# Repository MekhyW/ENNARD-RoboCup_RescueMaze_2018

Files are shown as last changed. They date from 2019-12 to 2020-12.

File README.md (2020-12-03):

# ENNARD - RoboCup Rescue Maze 2018
###### Autonomous navigation and victim-identifying robot, created to compete in RoboCup Junior Brazil Open 2018. The robot achieved 1st place out of 17 at the category, claiming the title of national champion.

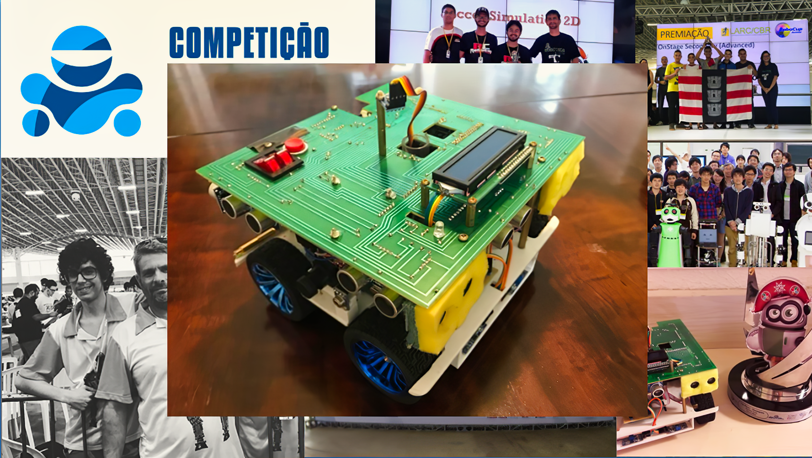
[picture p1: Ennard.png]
Ennard
### 

## Rescue Maze Preface

Rules can be found at: https://junior.robocup.org/rcj-rescue-maze/

" The robot needs to search through a maze for victims. The robot should not find the fastest path through the maze, instead it should explore as much of the maze as possible . The robot will get points for each victim found and will deliver a rescue kit close to the victim. The robot must avoid areas with a black floor.

Rescue Maze sub-league open to students from age 13 up to and including 19 years of age (age as of 1st of July).Team members may compete in Rescue Line twice (2 international events). After competing in Rescue Line twice, they must move to Rescue Maze. "

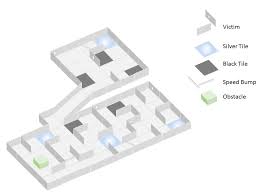
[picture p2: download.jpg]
Arena


## CAD Models

The folder 'models' contains all 3D files used and made during the prototyping/simulation phase of the project, using AutoCAD 2017.  Drawing-SALLES_X.dwg refers to different versions of the robot concept, while pá_X.dwg is a custom servo shovel design to facilitate rescue kit dropping. 

All printable files are in .stl files, and they are mechanically self-sufficient for the static assembly of the entire robot structure (aside from screws, standoffs, etc.).

## Hardware Components

The robot consists of:

1. 1x Arduino DUE microcontroller ARM board
2. 2x OpenMV Cam M7 machine vision boards (UART communication with the Arduino)
3. 4x Pololu 25D 12V HP metal gearmotors with 47:1 reduction (210RPM)
4. 4x Rotary hall-effect motor encoders
5. 4x Rubber wheels
6. 9x HC-SR04 ultrassonic rangefinder sensor modules
7. 2x MLX90614 infrared temperature sensor modules
8. 1x MPU6050 accelerometer sensor module
9. 1x HMC5883l magnetometer sensor module
10. 2x TCRT5000 active light reflectance sensor modules
11. 1x 16x2 segments LCD display with blue backlight
12. 1x Digital arcade button
13. 2x 12V LiPO batteries

## Team Description Paper 

In order to attend the Latin American Robotics Competition, every team must submit a TDP which shows the engineering strategies implemented. The following text (written in Brazillian Portuguese) summarizes these points in the IEEE text format: 'TDP' ---> TDP.pdf / TDP.docx

## Software

Code that is run during scored runs is stored in the 'ENNARD' folder. ENNARD.ino is the main C++ script, while low-level component interactions are handled by each header file.

'TestModes' contains debugging scripts for each component, and 'Cams' contains the multiple strategies tested for the identification of the new "Visual victims" (H, S and U letters), including template matching and blob segmentation.  

## Video Material

A few proof-of-concept videos were produced:

* Final version of the lower part of the chassis ---> https://www.youtube.com/watch?v=Bfc4bDW7wJo

- Wall Alignment (top view) ---> https://www.youtube.com/watch?v=RuqlHey5neY

- Wall Alignment (side view) ---> https://www.youtube.com/watch?v=VqffBqsZt2Q

- PID Control and ramp negotiation ---> https://www.youtube.com/watch?v=kQnzG5W4b-0

- Mecanum omnidirectional wheels (later changed to rubber wheels) ---> https://www.youtube.com/watch?v=znJ_pU6Sihw

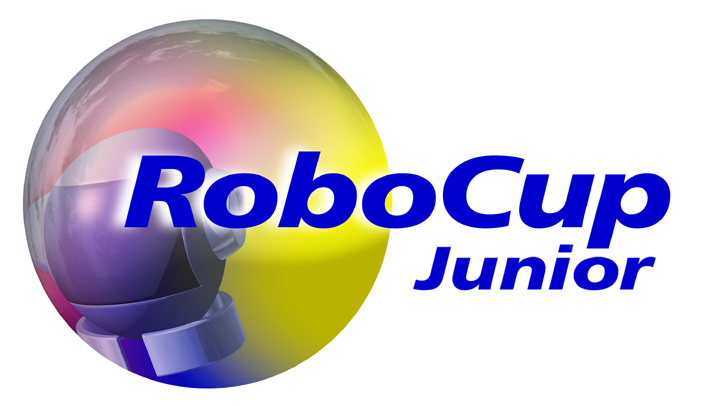
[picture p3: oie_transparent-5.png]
robocupjr


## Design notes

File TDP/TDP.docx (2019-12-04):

ENNARD – Robô de Rescue Maze da Escola de Robótica e Mecatrônica ABC Marcelo Salles

Felipe Catapano Emrich Melo, André Luiz Buzacarini Schulman, Marcelo Ribeiro Salles

Abstract ⎯ This article presents the development of an Arduino-controlled autonomous junior robot with emphasis on Latin American Robotics Competition 2018. All key components and critic design choices, as well as their purposes are detailed in this document.

I. INTRODUÇÃO

Pelo fato de estarmos iniciando na categoria e por complicações nas circunstâncias e envolvendo o projeto, nosso robô competidor para a LARC de 2017 (edição ocorrida em Curitiba, PR) fora construído com diversos problemas estruturais e soluções improvisadas. Utilizávamos motores de plástico energizados por um pack de pilhas (rompido internamente no meio da competição e consequentemente anulando uma de nossas rodadas), que eram fracos e tinham sua movimentação controlada por tempo (o que gerava um alto grau de imprecisão variável). Além disso a disposição dos sensores formava grandes pontos cegos.

Havendo, no entanto, superadas muitas das dificuldades e havendo observado inúmeros outros projetos de âmbito internacional em várias competições, o novo agente foi desenvolvido com a solução por completo da missão proposta em mente, que envolve a simulação de um salvamento de vítimas quentes e visuais em um ambiente de desastre inacessível a seres humanos.

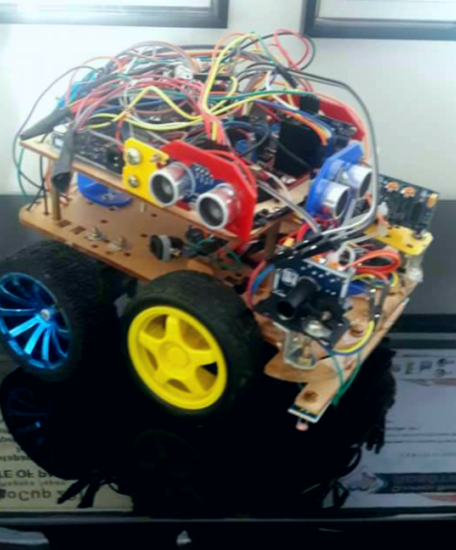
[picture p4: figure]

Imagem 1 - LESION, o robô de 2017

II. ESTRUTURA E CIRCUITOS

Com a utilização de uma impressora 3D, somos capazes de projetar e criar estruturas com encaixes perfeitos para os componentes de forma rápida e barata, portanto o chassi do robô foi desenhado com o software AutoCAD e impresso em PLA amarelo. O tubo e kits do nosso depositador de resgate, no entanto, foram feitos em acrílico para que não houvesse qualquer rebarba.

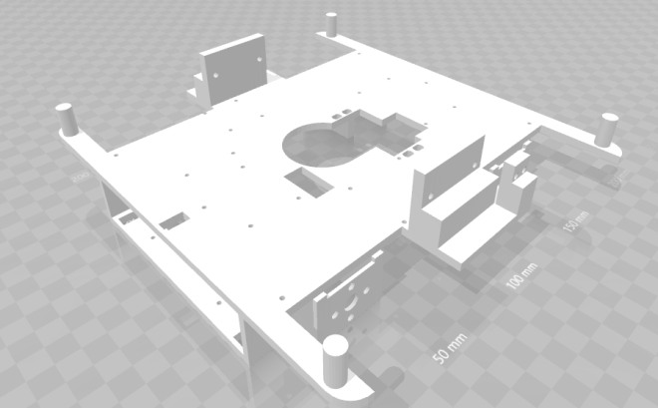
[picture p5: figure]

Imagem 2 - Chassi

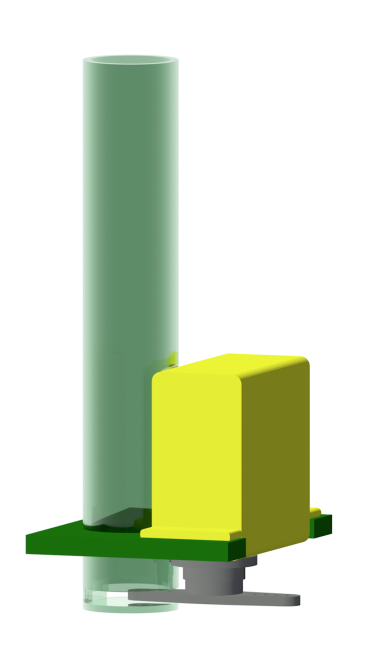
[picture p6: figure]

Imagem 3 - Depositador

Para similar finalidade, a de reduzir ao máximo a quantidade de fios e evitar problemas facilmente, percebemos que a impressão de circuitos integrados era essencial (também a desenhamos com AutoCAD). Duas PCBs ligadas por grupos de flat cables permitem que todas as trilhas possuam 1cm de largura e sejam consideravelmente expostas, reduzindo a possibilidade de erros.

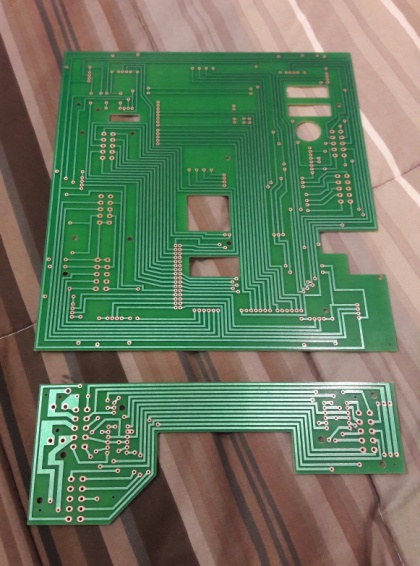
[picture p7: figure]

Imagem 4 – Circuitos integrados (primeiros protótipos)

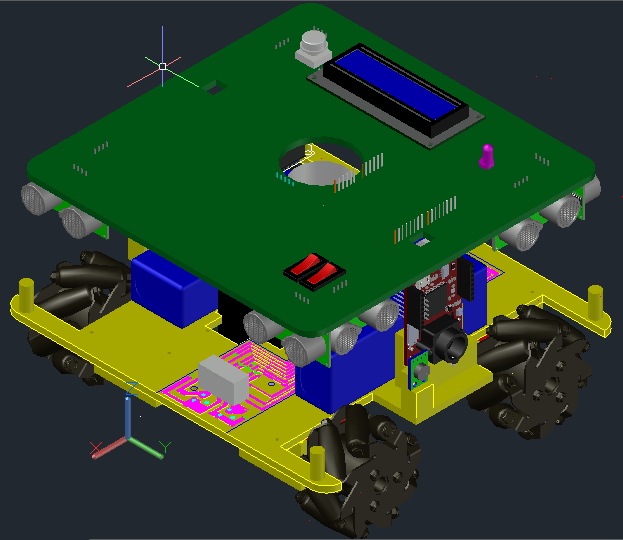
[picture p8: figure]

Imagem 5 – Robô completo simulado em CAD

III. CONTROLE E ATUAÇÃO

Arduino DUE foi a plataforma central escolhida pela simplicidade de uso, maior capacidade de variáveis e maior velocidade em relação a todos os outros arduinos, além da possibilidade de utilizar qualquer pino digital com interrupts, para melhor aproveitamento dos encoders presentes nos motores por exemplo (é a única placa da Arduino com arquitetura ARM). Ela (juntamente com os sensores conectados) é alimentada por um pack de baterias de Li-Ion, enquanto os motores são controlados por duas pontes-h L298n alimentadas em série por uma bateria de Li-Po separada.

Grande parte de nossa estratégia se dá pela escolha dos motores DC de 12V da Pololu, colocando a qualidade de alinhamento sensorial e velocidade de ultrapassagem de obstáculos acima da precisão absoluta garantida por servos motores. Um servo motor genérico MG996R (visto no suporte acima) foi utilizado para o depósito dos kits de resgate pelo baixo peso e custo para seu tamanho.

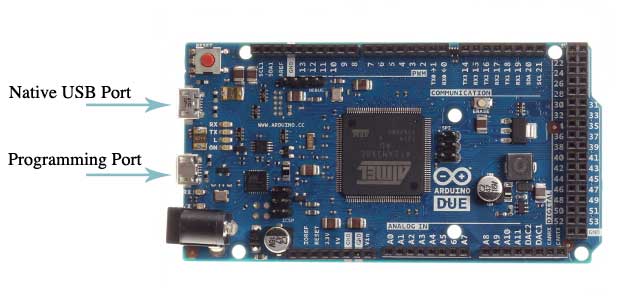
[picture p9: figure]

Imagem 6 – Arduino DUE

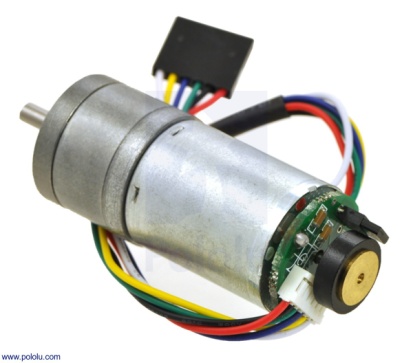
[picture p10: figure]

Imagem 7 – Motor com encoder

E para que fosse possível garantir total liberdade de movimento ao robô, as rodas ligadas aos motores são rodas mecanum da Nexus, de 6cm de diâmetro, adaptadas por calços usinados customizados para este fim. Seus rolos dispostos em 45 graus permitem a mesma característica de um sistema com quatro rodas omni tradicionais: Facilmente mover-se em qualquer direção (útil para alinhamentos rapidos e movimentos pequenos), porém com o benefício de poderem ser dispostas de maneira reta como rodas comuns.

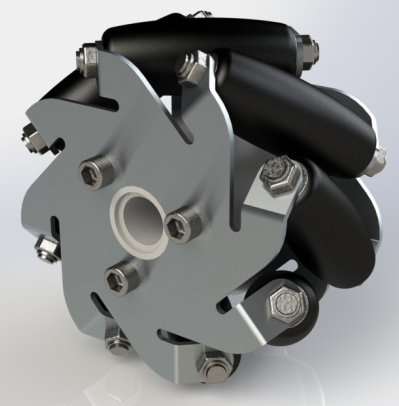
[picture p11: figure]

Imagem 8 – Roda mecanum

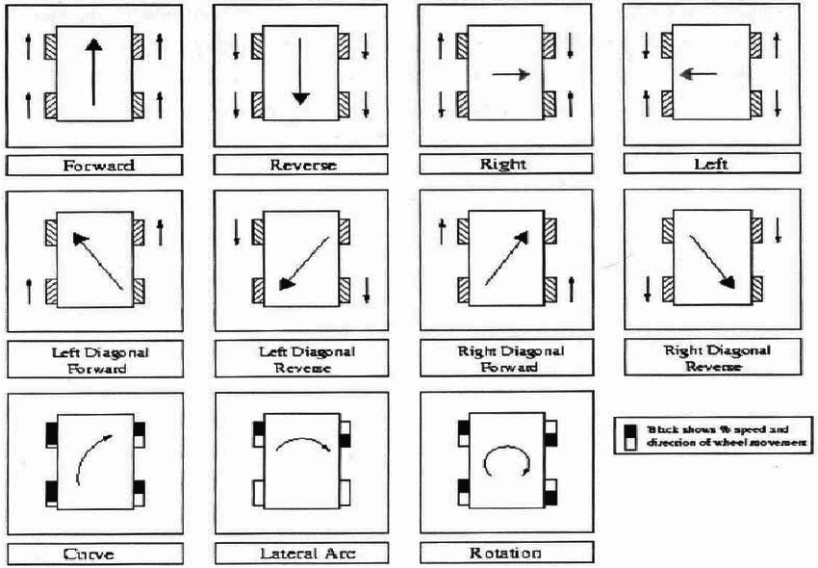
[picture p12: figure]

Imagem 9 – Esquema de movimentação com 4 rodas mecanum

IV. SENSORES E SINALIZAÇÃO

Para possibilitar a identificação das novas vítimas visuais, utilizamos duas pequenas placas programáveis OpenMV M7, ligadas ao arduino por comunicação UART. Por possuírem conexão externa e uma IDE própria, calibrar as placas pode ser feito de maneira direta e é possível retirá-las do robô facilmente caso necessário.

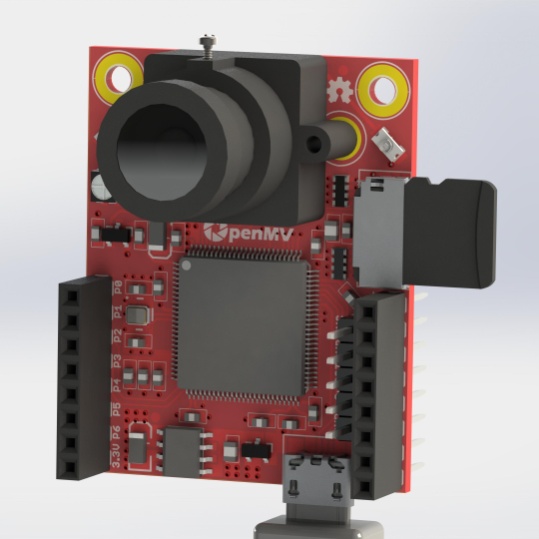
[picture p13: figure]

Imagem 10 – OpenMV com cartão SD

Escolhemos usar nove sensores ultrassônicos US-015 dispostos na horizontal para o sensoriamento das paredes pelo seu amplo campo de visão e precisão de medida acima dos comuns HC-SR04. Por suportarem o uso de interrupts digitais e não precisarmos ler todos as instâncias de uma única vez, seu elevado delay em relação a um sensor de luz torna-se desprezível.

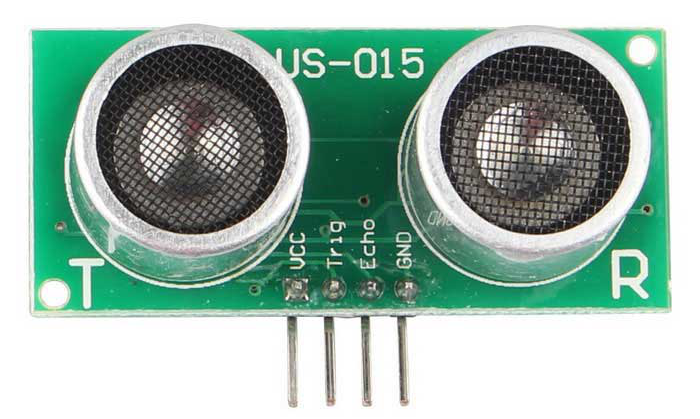
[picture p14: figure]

Imagem 11 – Sensor ultrassônico

A medição inercial é realizada por um único módulo 10DOF, o GY-87, que reúne giroscópio, acelerômetro(MPU6050, utilizado para percepção da rampa) e magnetômetro(HMC5883l, utilizado como bússola), além de um barômetro.

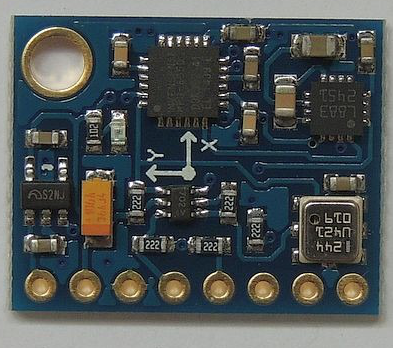
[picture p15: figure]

Imagem 12 – Unidade de Medição Inercial (UMI)

Para completar o sensoriamento utilizamos os populares MLX90614 para o reconhecimento das vítimas quentes, e dois sensores TCRT5000 para refletância do solo (perceber tiles pretos e tiles de checkpoint), além dos encoders presentes nos motores.

Há uma tela LCD de 16x2 divisões para feedback por texto, o que dispensa a constante necessidade de manter uma conexão com o computador para rastrear alguma variável ou processo, além de um LED multicolorido para sinalizar ações ao juíz e ao capitão da equipe com apenas um único sinal.

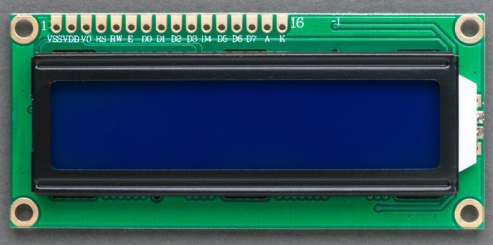
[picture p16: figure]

Imagem 13 – Display com luz de fundo azul

V. O SOFTWARE

Toda a programação do arduino foi escrita com a linguagem C++ utilizando o editor de texto Sublime Text 3 e compilada com a ArduinoIDE. Esta visa uma movimentação rápida e totalmente contínua do robô (isto é, sem um único delay) com alinhamentos constantes em relação às paredes. Um algoritmo de controle Proporcional Integral Derivativo (PID) será implementado para manter o robô centralizado ao subir e descer as rampas.

Um filtro Low Pass é aplicado na maioria das leituras para que não haja muitos ruídos entre as mesmas, e .

Para o path planning (decisão de quais direções a tomar dentro do labirinto), utilizamos o algoritmo de Tremaux como base (virar à direita é priorizado em relação a seguir em frente ou virar à esquerda, com objetivo de “contornar” o mapa), e a complementamos com um algoritmo de Floodfill modificado (priorização de áreas ainda não exploradas na rodada e retorno ao quadrado inicial pelo caminho mais curto conhecido, sem a necessidade de rotinas secundárias ou um mapeamento da configuração do labirinto). Na partida, Um mapa virtual é criado com todos os nodos incialmente zerados, e, após o robô passar de um nodo a outro, caso o valor deste for zero ele passa a ser o sucessor do valor do nodo anterior.

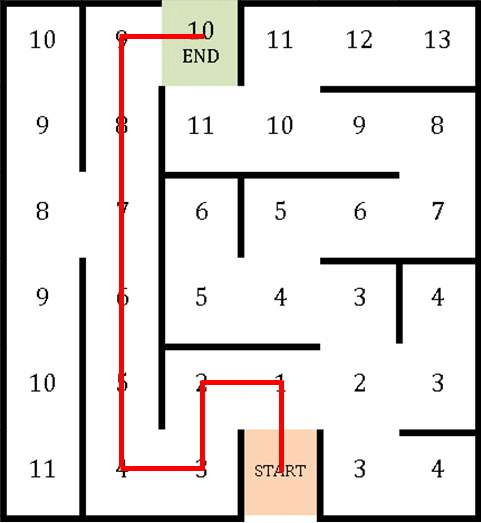
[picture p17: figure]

Imagem 14 – Exemplo de FloodFill resolvendo um labirinto com saída

A programação das câmeras é escrita em Python (elas funcionam com o sistema operacional MicroPython) pela própria IDE da OpenMV, e consiste na comparação entre cada frame capturado pelo módulo embutido e pequenas fotos de letras presentes na memória flash (algoritmo conhecido como Template Matching). Parâmetros básicos de imagem como exposição, equilíbrio de branco, etc.são automaticamente normalizados pela câmera, assim reduzindo todos os parâmetros humanamente ajustados a apenas três filtros de 0 a 1, um para cada letra a ser identificada.

VI. ARENA DE TESTES

Percebemos durante o planejamento deste projeto que a construção de um ambiente que simule situações oficialmente presente nas competições é essencial para uma boa preparação da estratégia. Portanto a equipe investiu em uma arena que seguisse fielmente as regras, apesar do seu real tamanho quando montada, para podermos testar aspectos do robô antes mesmo de este estar funcionando por completo.

A madeira é o material ideal utilizado na grande maioria desses eventos pelo seu baixo custo, resistência e facilidade de produzir encaixes lineares. Portanto toda a estrutura da arena de testes é feita com este material. Lombadas, garrafas de areia, tijolos, varetas e outros obstáculos estão a disposição para criar cenários com um nível de desafio equivalente ou maior ao visto na RoboCup Junior.

VII. CONCLUSÃO

Foi possível perceber que a parte mais importante de um projeto deste porte é a fase de pesquisa, que nos permitiu estabelecer contato com diversas opções de dispositivos de melhor performance para a realização desta e de outras tarefas da engenharia mecatrônica e da ciência da computação, descartar estratégias/metodologias que demonstraram menos resultados antes mesmo do início da montagem do robô, comunicar-se com outros competidores e no geral evoluir como estudantes juniores.

VIII. AGRADECIMENTOS

A equipe ENNARD Salles gostaria muito de agradecer à Escola de Robótica, a seus professores e envolvidos, e aos nossos pais por nos propiciar esta incrível oportunidade e ferramentas para trabalhar com o Resgate e aos ex-competidores Leonardo Santander da Silva e Ivan Seidel Gomes pelas experiências compartilhadas e por serem de grande fonte de inspiração.

IX. REFERÊNCIAS
[1] Escola de Robótica e Mecatrônica ABC Marcelo Salles. Disponível em: http://www.roboticaabc.com.br
[2] RoboCup Junior. Disponível em: http://junior.robocup.org
[3] Arduino platform. Disponível em: https://www.arduino.cc
[4] OpenMV platform. Disponível em: https://openmv.io
[5] MicroPython. Disponível em: https://micropython.org
[6] NEXUS Robot. Disponível em: http://www.nexusrobot.com (https://pt.wikipedia.org/wiki/Omnidirecional)
[7] Impressão 3D. Disponível em:

https://pt.wikipedia.org/wiki/Impressão_3D

[8] AutoCAD. Disponível em: https://www.autodesk.com.br/products/autocad/overview
[9] Sublime Text. Disponível em: https://www.sublimetext.com
[10] Ponte H. Disponível em: https://pt.wikipedia.org/wiki/Ponte_H
[11] Motores Pololu de 25Dmm. Disponível em: https://www.pololu.com/category/115/25d-mm-metal-gearmotors
[12] Servo Motor. Disponível em: https://pt.wikipedia.org/wiki/Servomotor
[13] US-015 vs HC-SR04. Disponível em: https://www.youtube.com/watch?v=aLkkAsrSibo&t=219s
[14] Display de Cristal Líquido (LCD) . Disponível em: https://pt.wikipedia.org/wiki/LCD
[15] IMU. Disponível em: https://en.wikipedia.org/wiki/Inertial_measurement_unit
[16] Ultrassônico. Disponível em: https://pt.wikipedia.org/wiki/Ultrassom
[17] Temperatura Infravermelha. Disponível em: http://guias.oxigenio.com/como-funciona-um-termometro-infravermelho
[18] Luz Infravermelha. Disponível em: https://pt.wikipedia.org/wiki/Radia%C3%A7%C3%A3o_infravermelha
[19] Algoritmo Trémaux. Disponível em: https://pt.wikipedia.org/wiki/Algoritmo_de_Tremaux
[20] Algoritmo Floodfill. Disponível em: https://en.wikipedia.org/wiki/Flood_fill
[21] Material para arena de testes. Disponível em: http://www.leomadeiras.com.br

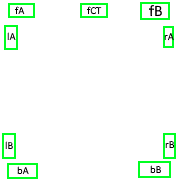
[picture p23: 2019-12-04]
ultrasound_pos.png

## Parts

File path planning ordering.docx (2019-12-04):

- Beco sem saída?
- Apenas posso ir pra frente, direita ou esquerda (sem contar atrás)?
- Tile inexplorado a direita?
- Tile inexplorado a frente?
- Tile inexplorado a esquerda?
- BFS retornou o tile inexplorado mais próximo?
- Seguir menor floodfill.

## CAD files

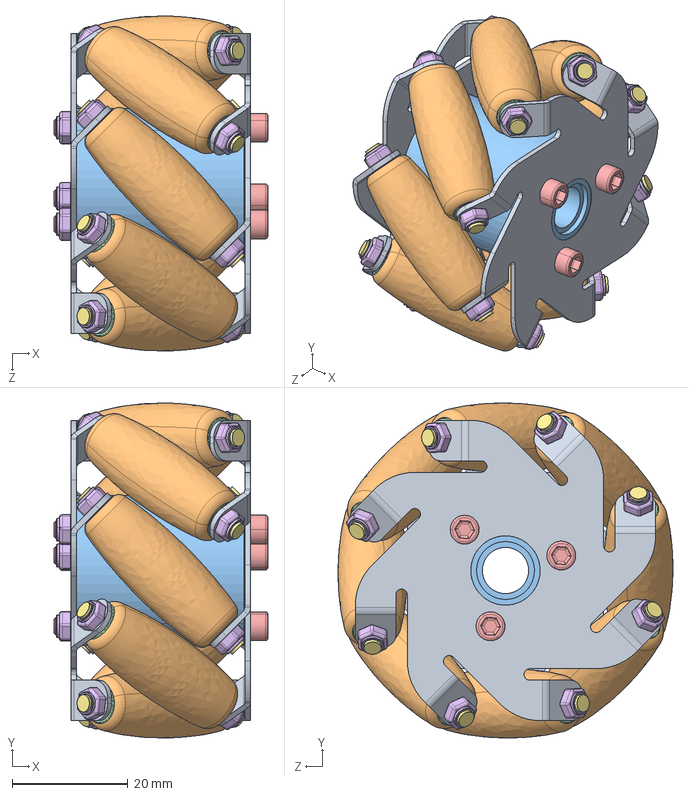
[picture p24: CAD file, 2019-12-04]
models/60mm-aluminium-mecanum-wheel-nexus-robot-1.snapshot.15/Nexus 60mm Mecanum/STEP/Mecanum_Wheel_60mm_Left_ASM_AP203.STEP
37.0 x 58.0 x 58.0 mm
plate_1_Varsayilan x 2
roller_Varsayilan x 8
inner_cylinder_Varsayilan
liner_Varsayilan x 16
3x35_screw_Varsayilan x 3
3mm_bolt_Varsayilan x 19
two_sided_screw_Varsayilan x 8

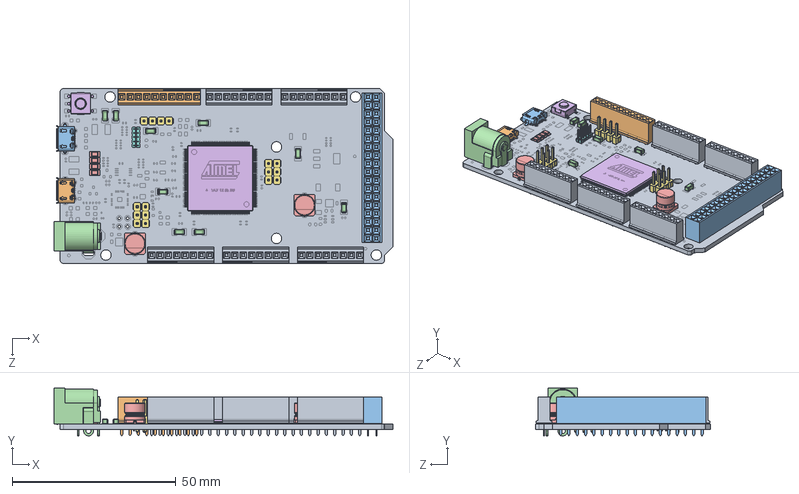
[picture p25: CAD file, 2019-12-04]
models/arduino-due-1.snapshot.10/ARDUINO DUE.SLDASM
103.5 x 14.6 x 53.3 mm
PCB - Arduino
MicroUSB B - Hirose - ZX62D-B-5P8
MicroUSB AB - Hirose - ZX62D-AB-5P8
Power Jack - Kycon - KLDHCX-0202-A
LED - Kingbright - KPT-3216EC x 4
Microchip - Atmel - SAM3X8EAU
Berg Header - 2.54 x 2 x 8
Berg Header - 1.27 x 10
Berg Header Receptacle 2.54 x 8 - FCI - 66951-008LF x 5
Berg Header Receptacle 2.54 x 10 - FCI - 66951-010LF
Berg Header Receptacle 2.54 x 36 - FCI - 66953-018LF
Capacitor x 9
Capacitor - Nichicon - UUR1C101MCL1GS x 2
Switch - ESwitch - TLE3303

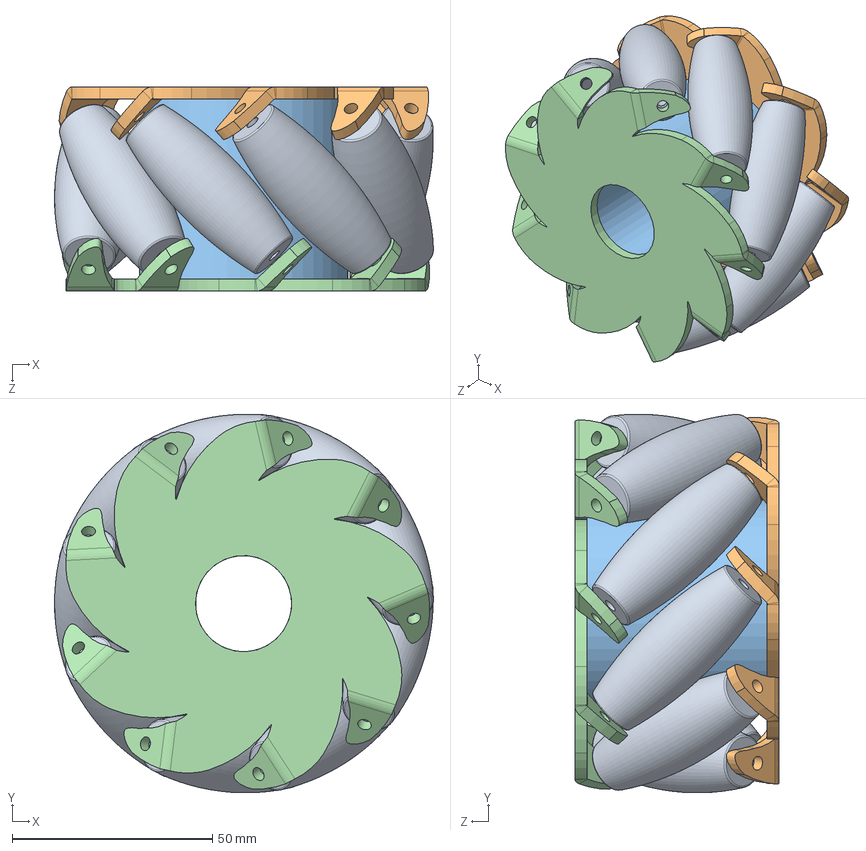
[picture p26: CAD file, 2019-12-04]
models/mecanum-omni-wheels-1.snapshot.1/Mecanum wheels/MECANUM WHEELS.SLDASM
94.5 x 94.4 x 51.0 mm
mec roller x 9
MECANUM 1
mid
MECANUM 1 - Copy (3)

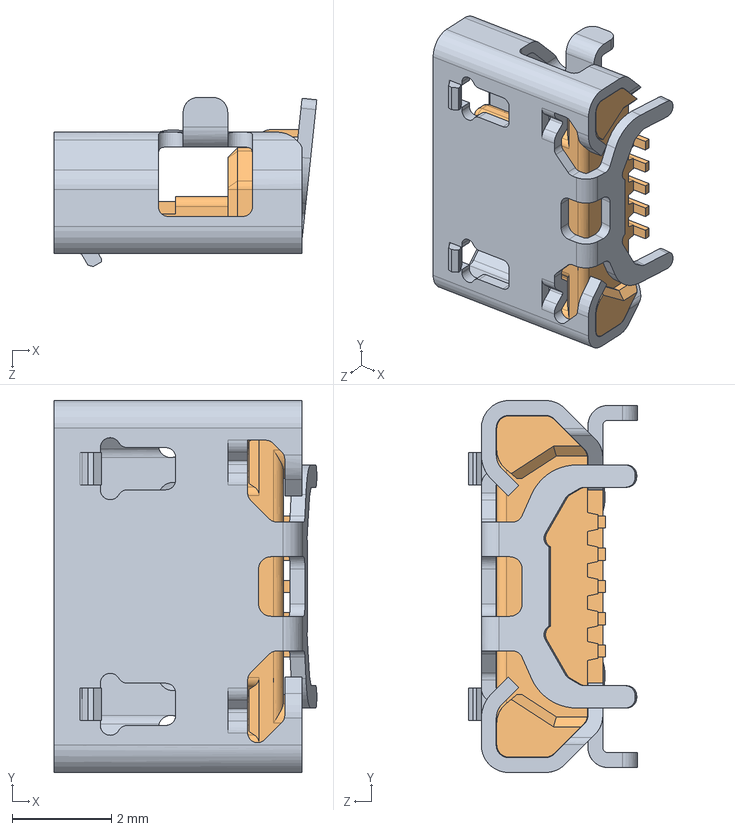
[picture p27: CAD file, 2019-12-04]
models/openmv3_export/Components/UJ2-MIBH2-4-SMT.SLDASM
5.29 x 7.50 x 3.41 mm
UJ2-MIBH2-4-SMT_01
UJ2-MIBH2-4-SMT_02

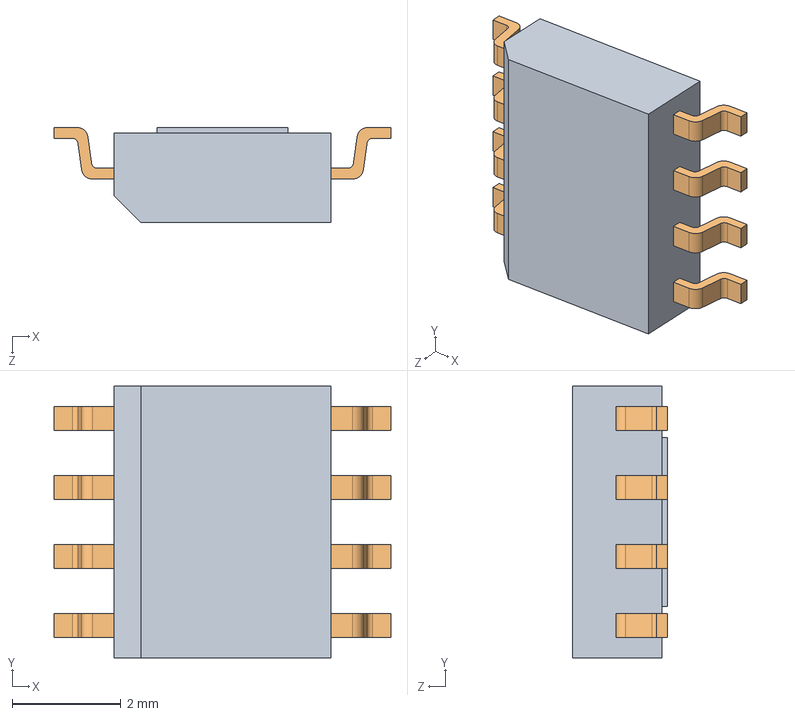
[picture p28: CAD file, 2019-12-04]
models/openmv3_export/Components/User Library-HSOP8.SLDASM
6.20 x 5.00 x 1.75 mm
User Library-HSOP8_part hsop8
User Library-HSOP8_Fuss_hsop8 x 12

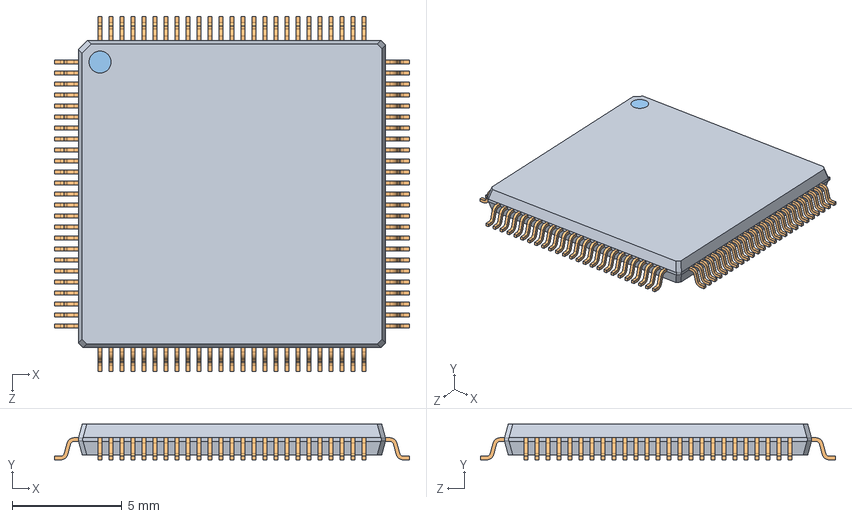
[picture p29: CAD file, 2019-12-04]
models/openmv3_export/Components/User Library-LQFP100-3.sldasm
16.1 x 1.63 x 16.1 mm
User Library-LQFP100-3_case
User Library-LQFP100-3_pin x 100
User Library-LQFP100-3_circle

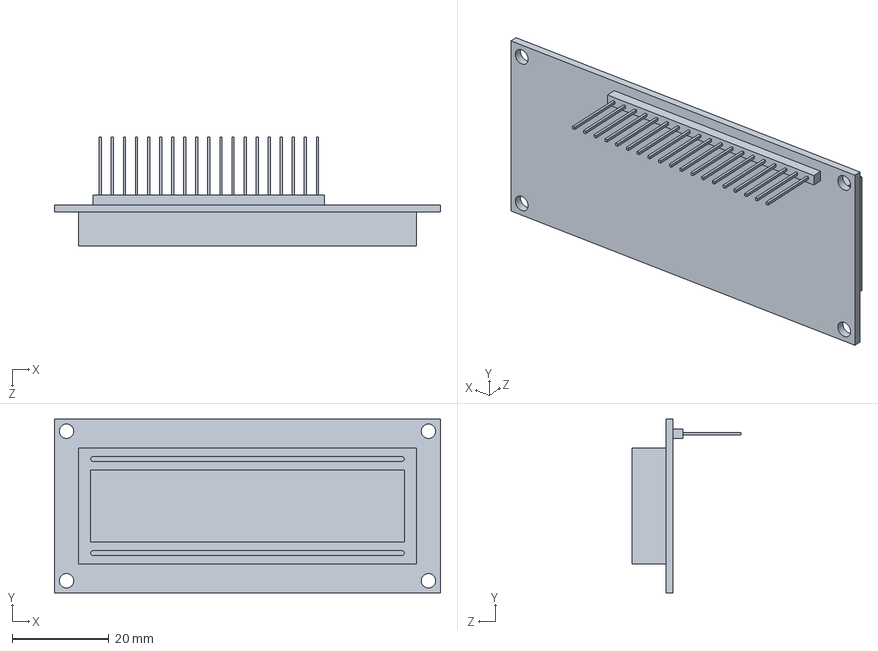
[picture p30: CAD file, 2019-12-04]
models/16x2-lcd-display-2.snapshot.1/16x2 Lcd display dsgn arch 2016-edit-00.SLDPRT
80.0 x 36.0 x 22.5 mm

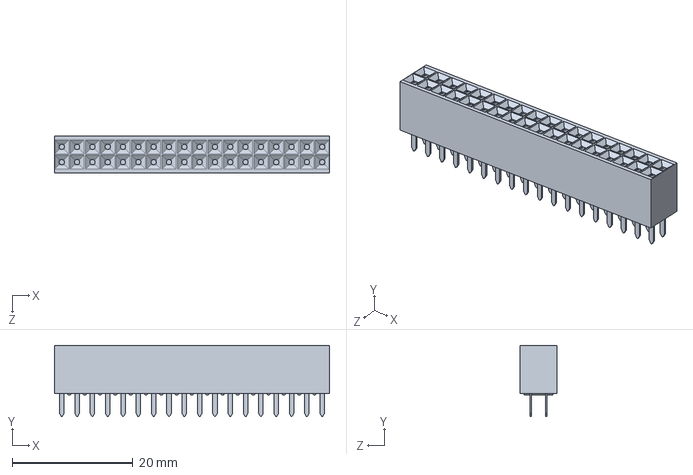
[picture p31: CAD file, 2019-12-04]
models/arduino-due-1.snapshot.10/Arduino Due/Berg Header Receptacle 2.54 x 36 - FCI - 66953-018LF.SLDPRT
45.6 x 11.8 x 6.10 mm

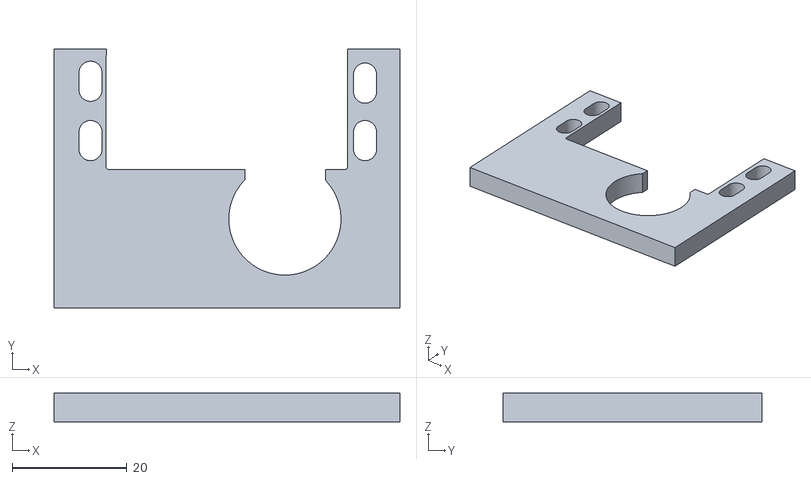
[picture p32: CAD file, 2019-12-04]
models/base Felipe Depositador terminado.stl
60.2 x 45.1 x 5.00

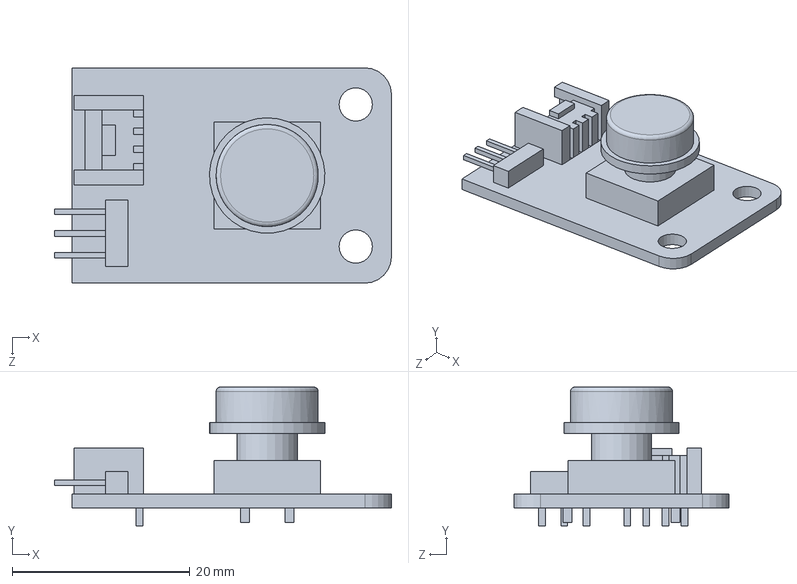
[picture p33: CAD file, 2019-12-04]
models/big-button-module-1.snapshot.2/Big Button.SLDPRT
37.9 x 15.7 x 24.2 mm

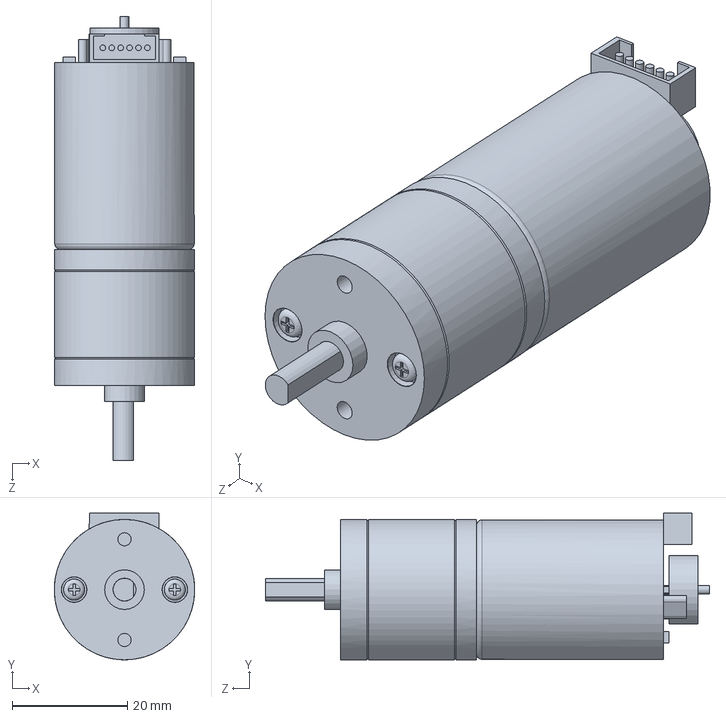
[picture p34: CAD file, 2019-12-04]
models/dc-motor-with-encoder-1.snapshot.1/Motor.SLDPRT
24.4 x 25.5 x 77.1 mm

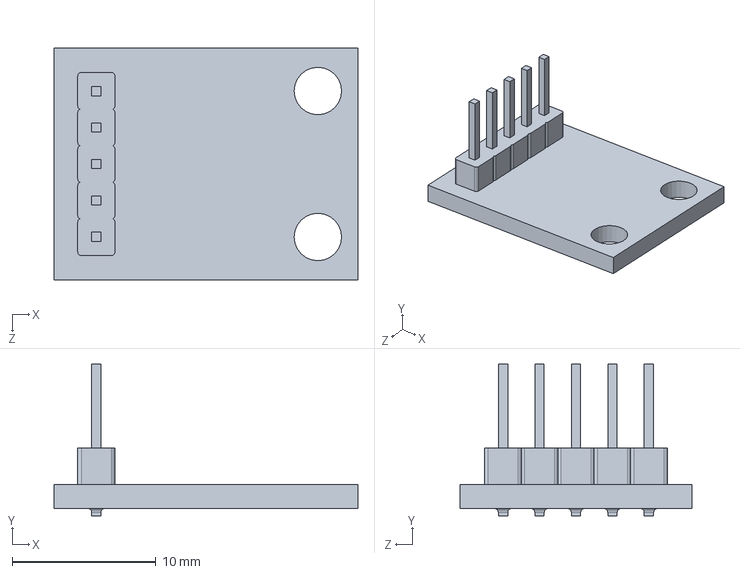
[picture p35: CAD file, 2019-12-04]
models/gy-61-adxl335-accelerometer-1.snapshot.7/GY-61_Accelerometer.SLDPRT
21.2 x 10.6 x 16.2 mm

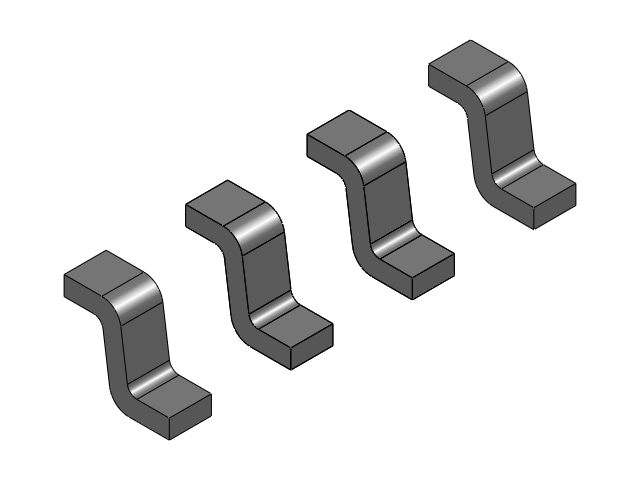
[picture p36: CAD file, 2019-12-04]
models/openmv3_export/Components/User Library-HSOP8_Assy fuss hsop8.SLDASM
User Library-HSOP8_Fuss_hsop8 x 6

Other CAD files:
models/60mm-aluminium-mecanum-wheel-nexus-robot-1.snapshot.15/Nexus 60mm Mecanum/STEP/Mecanum_Wheel_60mm_Right_ASM_AP214.STEP
models/60mm-aluminium-mecanum-wheel-nexus-robot-1.snapshot.15/Nexus 60mm Mecanum/STEP/Mecanum_Wheel_60mm_Right_ASM_AP203.STEP
models/60mm-aluminium-mecanum-wheel-nexus-robot-1.snapshot.15/Nexus 60mm Mecanum/Mecanum_Wheel_60mm_Right_ASM.SLDASM
models/60mm-aluminium-mecanum-wheel-nexus-robot-1.snapshot.15/Nexus 60mm Mecanum/STEP/Mecanum_Wheel_60mm_Left_ASM_AP214.STEP
models/60mm-aluminium-mecanum-wheel-nexus-robot-1.snapshot.15/Nexus 60mm Mecanum/Mecanum_Wheel_60mm_Left_ASM.SLDASM
models/60mm-aluminium-mecanum-wheel-nexus-robot-1.snapshot.15/Nexus 60mm Mecanum/3mm_bolt.SLDPRT
models/60mm-aluminium-mecanum-wheel-nexus-robot-1.snapshot.15/Nexus 60mm Mecanum/3x35_screw.SLDPRT
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

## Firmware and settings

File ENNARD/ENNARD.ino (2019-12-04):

// ENNARD Rescue Maze Robot  (former Project Linker)
// Escola de Robótica ABC Marcelo Salles
// VERSION: 7.8
#include <Wire.h>
#include "Display.h"
#include "Orientation.h"
#include "Temperature.h"
#include "Reflection.h"
#include "Ultrasound.h"
#include "PID.h"
#include "Motors.h"
#include "Encoders.h"
#include "Cameras.h"
#include "Map.h"


void setup() {
  Serial.begin(9600);
  DisplayInitialize();
  CamsInitialize();
  ReflectionInitialize();
  TemperatureInitialize();
  MotorsInitialize();
  PressToStart(true);
  IMUInitialize();
  floodfill[currentfloor][PositionX][PositionY]=1;
}


void loop() {
  ResetEncoders();
  while(EncPulseEA<TileDist || EncPulseEB<TileDist || EncPulseDA<TileDist || EncPulseDB<TileDist){
    UpdateEncoders();
  	CheckBackup();
    ReadUltrassound(true, true, true, true, true, true, true, true, true);
    if(USFrontCT<15 && USFrontB<15){
      Display("", "loop break");
      MotorsStop();
      delay(500);
      MoveBackwards(150);
      delay(100);
      MotorsStop();
      break;
    }
    CheckVictim();
    if(USFrontA<15 && USFrontCT>30 && USFrontB>30 && USLeftA>30 && (currentfloor!=1||PositionX!=15||PositionY!=15)){
      AvoidLeft();
    } 
    if(USFrontB<15 && USFrontCT>30 && USFrontA>30 && USRightA>30 && (currentfloor!=1||PositionX!=15||PositionY!=15)){
      AvoidRight();
    }
    ReadReflection();
    if(ReflectLeft>TrapLimit && ReflectRight>TrapLimit){
      BlackZone();
      break;
    }
    if(currentfloor==1&&PositionX==15&&PositionY==15){
      MoveForward(200);
    } else {
      MoveForwardPID(200); 
    }
    Display(String(ReflectLeft), String(ReflectRight));
  }
  NextMove();
}









void Align(){
  LockEncoders();
  ReadUltrassound(true, true, true, true, true, true, true, true, true);
  if(USFrontCT<99 && ((USFrontA==99&&USFrontB<99)||(USFrontA<99&&USFrontB==99))){
    Display("out of bounds", "");
    if(USFrontA<USFrontB){
      AvoidRight();
    } else if(USFrontB<USFrontA){
      AvoidLeft();
    }
    ReadUltrassound(true, true, true, true, true, true, true, true, true);
  }
  if(USBackA<30 && USBackB<30){
    Display("bump back", "");
    MoveBackwards(150);
    while((USBackA>13&&USBackA<30)||(USBackB>13&&USBackB<30)){
      MoveBackwards(150);
      ReadUltrassound(false, false, false, false, false, true, true, false, false);
      CheckVictim();
    }
    delay(200);
    MoveForward(150);
    delay(150);
    MotorsStop();
  } else if(USFrontCT<30 && USFrontA<30 && USFrontB<30){
    MotorsStop();
    Display("bump fwd", "");
    MoveForward(150);
    while((USFrontA>13&&USFrontA<30)||(USFrontB>13&&USFrontB<30)){
      MoveForward(150);
      ReadUltrassound(true, false, true, false, false, false, false, false, false);
      CheckVictim();
    }
    delay(200);
    MoveBackwards(150);
    delay(150);
    MotorsStop();
  }
  UnlockEncoders();
}



void AvoidLeft(){
  LockEncoders();
  RotateLeft(150);
  delay(200);
  MoveBackwards(150);
  delay(200);
  RotateRight(150);
  delay(300);
  MoveForward(150);
  delay(200);
  RotateLeft(150);
  delay(150);
  UnlockEncoders();
}

void AvoidRight(){
  LockEncoders();
  RotateRight(150);
  delay(200);
  MoveBackwards(150);
  delay(200);
  RotateLeft(150);
  delay(300);
  MoveForward(150);
  delay(200);
  RotateRight(150);
  delay(150);
  UnlockEncoders();
}


void Wobble(){
  LockEncoders();
  ReadUltrassound(false, false, false, true, true, false, false, true, true);
  if(USLeftA>17 && USLeftA<30 && USLeftB<30){
      Display("wobble left", "");
      while(USLeftA>17 && USLeftA<30 && USLeftB<30){
        ReadUltrassound(false, false, false, false, false, false, false, false, true);
        RotateRight(150);
        delay(50);
        MoveBackwards(200);
        delay(50);
        RotateLeft(150);
        delay(50);
        MoveForward(200);
        delay(50);  
      }
  } else if(USRightA>17 && USRightA<30 && USRightB<30){
      Display("wobble right", "");
      while(USRightA>17 && USRightA<30 && USRightB<30){
        ReadUltrassound(false, false, false, true, false, false, false, false, false);
        RotateLeft(150);
        delay(50);
        MoveBackwards(200);
        delay(50);
        RotateRight(150);
        delay(50);
        MoveForward(200);
        delay(50);  
      }
  } else if(USRightA<14 && USRightB<30){
      Display("wobble left", "");
      while(USRightA<14 && USRightB<30){
        ReadUltrassound(false, false, false, true, false, false, false, false, false);
        RotateRight(150);
        delay(50);
        MoveBackwards(200);
        delay(50);
        RotateLeft(150);
        delay(50);
        MoveForward(200);
        delay(50);  
      }
  } else if(USLeftA<14 && USLeftB<30){
      Display("wobble right", "");
      while(USLeftA<14 && USLeftB<30){
        ReadUltrassound(false, false, false, false, false, false, false, false, true);
        RotateLeft(150);
        delay(50);
        MoveBackwards(200);
        delay(50);
        RotateRight(150);
        delay(50);
        MoveForward(200);
        delay(50);  
      }
  }
  UnlockEncoders();
}


void Retreat(){
  MotorsStop();
  EA.write(EncPulseEA*1.2);
  EB.write(EncPulseEB*1.2);
  DA.write(EncPulseDA*1.2);
  DB.write(EncPulseDB*1.2);
  while(EncPulseAvg>0){
    MoveBackwards(200);
    EncPulseEA=EA.read();
    EncPulseEB=EB.read();
    EncPulseDA=DA.read();
    EncPulseDB=DB.read();
    EncPulseAvg=(EncPulseEA+EncPulseEB+EncPulseDA+EncPulseDB)/4;
    CheckVictim();
    CheckBackup();
  }
  MotorsStop();
}


void TurnLeft(){
  Wobble();
  MotorsStop();
  MotorsStop();
  MotorsStop();
  Display("<<<", "");
  ResetEncoders();
  while(EncPulseEA<TurnDist || EncPulseEB<TurnDist || EncPulseDA<TurnDist || EncPulseDB<TurnDist){
    RotateLeft(200);
    UpdateEncoders();
    CheckBackup();
    if(EncPulseAvg<(TurnDist/3)){
      CheckVictim();
    }
  }
  MotorsStop();
  if(Quadrant==1){
    Quadrant=4;
  } else if(Quadrant==2){
    Quadrant=3;
  } else if(Quadrant==3){
    Quadrant=1;
  } else if(Quadrant==4){
    Quadrant=2;
  }
  RelativeXY();
  ResetEncoders();
  Wobble();
  Align();
  Wobble();
}



void TurnRight(){
  Wobble();
  MotorsStop();
  MotorsStop();
  MotorsStop();
  Display(">>>", "");
  ResetEncoders();
  while(EncPulseEA<TurnDist || EncPulseEB<TurnDist || EncPulseDA<TurnDist || EncPulseDB<TurnDist){
    RotateRight(200);
    UpdateEncoders();
    CheckBackup();
    if(EncPulseAvg<(TurnDist/3)){
      CheckVictim();
    }
  }
  MotorsStop();
  if(Quadrant==1){
    Quadrant=3;
  } else if(Quadrant==2){
    Quadrant=4;
  } else if(Quadrant==3){
    Quadrant=2;
  } else if(Quadrant==4){
    Quadrant=1;
  }
  RelativeXY();
  ResetEncoders();
  Wobble();
  Align();
  ReadUltrassound(false, false, false, true, true, false, false, true, true);
  Wobble();
}


void TurnBackwards(){
  if(USLeftA>=USRightA){
    TurnLeft();
    TurnLeft();
  } else {
    TurnRight();
    TurnRight();
  }
}


void CheckVictim(){
      ReadTemperature();
      ReadCams();
      if(TemperatureL>=VHeatThreshold && USLeftA<30 && USLeftB<30 && ((EncPulseAvg<=TileDist/2&&heatmap[currentfloor][PositionX][PositionY]==0)||(EncPulseAvg>TileDist/2&&heatmap[currentfloor][ForwardX][ForwardY]==0))){
        Victim(1, 1);
      } else if(TemperatureR>=VHeatThreshold && USRightA<30 && USRightB<30 && ((EncPulseAvg<=TileDist/2&&heatmap[currentfloor][PositionX][PositionY]==0)||(EncPulseAvg>TileDist/2&&heatmap[currentfloor][ForwardX][ForwardY]==0))){
        Victim(1, 2);
      } else if((MVLeftChar==Decode_H || MVLeftChar==Decode_S || MVLeftChar==Decode_U) && USLeftA<30 && USLeftB<30 && USLeftA>13 && (EncPulseAvg<(TileDist*0.25)||EncPulseAvg>(TileDist*0.75)) && ((EncPulseAvg<=TileDist/2&&heatmap[currentfloor][PositionX][PositionY]==0)||(EncPulseAvg>TileDist/2&&heatmap[currentfloor][ForwardX][ForwardY]==0))){
        if(MVLeftChar==Decode_H){
          Victim(2, 1);
        }
        if(MVLeftChar==Decode_S){
          Victim(3, 1);
        }
        if(MVLeftChar==Decode_U){
          Victim(4, 1);
        }
      } else if((MVRightChar==Decode_H || MVRightChar==Decode_S || MVRightChar==Decode_U) && USRightA<30 && USRightB<30 && USRightA>13 && (EncPulseAvg<(TileDist*0.25)||EncPulseAvg>(TileDist*0.75)) && ((EncPulseAvg<=TileDist/2&&heatmap[currentfloor][PositionX][PositionY]==0)||(EncPulseAvg>TileDist/2&&heatmap[currentfloor][ForwardX][ForwardY]==0))){
        if(MVRightChar==Decode_H){
          Victim(2, 2);
        }
        if(MVRightChar==Decode_S){
          Victim(3, 2);
        }
        if(MVRightChar==Decode_U){
          Victim(4, 2);
        }
      }
}


void Victim(int type, int side){
  MotorsStop();
  if(type==1){
    Display("Victim Found:", "Heated");
  } else if(type==2){
    Display("Victim Found:", "Visual HARMED");
  } else if(type==3){
    Display("Victim Found:", "Visual STABLE");
  } else if(type==4){
    Display("Victim Found:", "Visual UNHARMED");
  }
  if(EncPulseAvg<=TileDist/2){
    heatmap[currentfloor][PositionX][PositionY]=1;
  } else {
    heatmap[currentfloor][ForwardX][ForwardY]=1;
  }
  if(type==1){
    Blink_for_five();
  }
  if(type==4 || KitCounter>=12){
    Blink_for_five();
  } else if(side==1){
    DeployKitLeft();
    if(type==2){
      DeployKitLeft();
    }
  } else if(side==2){
    DeployKitRight();
    if(type==2){
      DeployKitRight();
    }
  }
}


void BlackZone(){
  MotorsStop();
  Display("Trap ahead", String(EncPulseAvg));
  Retreat();
  trapmap[currentfloor][ForwardX][ForwardY]=1;
}


void Ramp(){
  if(Inclination>=110){
    Display("Ramping", "UP");
    while(USFrontCT>15 || USFrontA>15 || USFrontB>15){
      ReadUltrassound(true, true, true, true, true, false, false, true, true);
      MoveForwardPID(255);
      CheckBackup();
    }
    currentfloor++;
    if(floodfill[currentfloor][BackwardsX][BackwardsY]==0){
      floodfill[currentfloor][BackwardsX][BackwardsY]=1;
    }
  } else if(Inclination<=70){
    Display("Ramping", "DOWN");
    while(USFrontCT>15 || USFrontA>15 || USFrontB>15){
      ReadUltrassound(true, true, true, true, true, false, false, true, true);
      MoveForwardPID(130);
      CheckBackup();
    }
    currentfloor--;
    if(floodfill[currentfloor][BackwardsX][BackwardsY]==0){
      floodfill[currentfloor][BackwardsX][BackwardsY]=1;
    }
  }
}



void NextMove(){
  //CHECKS
  if(EncPulseAvg>=(TileDist/2)){
    CalculateDisplacement();
    ResetEncoders();
  }
  if(USLeftA<30 && USRightA<30 && USFrontCT>30){
    MotorsStop();
    delay(1000);
    ReadAccel();
    if(Inclination>=110 || Inclination<=70){
      Ramp();
    } else {
      CheckVictim();
    }
  }
  Align();
  ReadReflectionPure();
  if(ReflectLeft<=CheckpointLimit && ReflectRight<=CheckpointLimit && (PositionX!=PositionXBackup || PositionY!=PositionYBackup)){
      UpdateBackup();
  }
  bool IsForwardAvailable=true;
  bool IsRightAvailable=true;
  bool IsLeftAvailable=true;
  bool IsBackwardsAvailable=true;
  ReadUltrassound(false, true, false, true, true, true, true, true, true);
  if(USFrontCT<30 || trapmap[currentfloor][ForwardX][ForwardY]==1){
    IsForwardAvailable=false;
  }
  if((USLeftA<30&&USLeftB<30) || trapmap[currentfloor][LeftX][LeftY]==1){
    IsLeftAvailable=false;
  }
  if((USRightA<30&&USRightB<30) || trapmap[currentfloor][RightX][RightY]==1){
    IsRightAvailable=false;
  }
  if(USBackA<30 || USBackB<30 || trapmap[currentfloor][BackwardsX][BackwardsY]==1){
    IsBackwardsAvailable=false;
  }
  //EXIT
  if(PositionX==15 && PositionY==15 && currentfloor==1 && (floodfill[currentfloor][ForwardX][ForwardY]>0||IsForwardAvailable==false) && (floodfill[currentfloor][RightX][RightY]>0||IsRightAvailable==false) && (floodfill[currentfloor][LeftX][LeftY]>0||IsLeftAvailable==false) && (floodfill[currentfloor][BackwardsX][BackwardsY]>0||IsBackwardsAvailable==false)){
    Display("EXIT...", "");
    MotorsStop();
    Blink_for_five();
    Blink_for_five();
  }
  //DECISION
  if(IsRightAvailable==true && (IsForwardAvailable==false||(floodfill[currentfloor][RightX][RightY]<=floodfill[currentfloor][ForwardX][ForwardY])) && (IsBackwardsAvailable==false||(floodfill[currentfloor][RightX][RightY]<=floodfill[currentfloor][BackwardsX][BackwardsY])) && (IsLeftAvailable==false||(floodfill[currentfloor][RightX][RightY]<=floodfill[currentfloor][LeftX][LeftY]))){
    TurnRight();
  } else if(IsForwardAvailable==true && (IsRightAvailable==false||(floodfill[currentfloor][ForwardX][ForwardY]<=floodfill[currentfloor][RightX][RightY])) && (IsBackwardsAvailable==false||(floodfill[currentfloor][ForwardX][ForwardY]<=floodfill[currentfloor][BackwardsX][BackwardsY])) && (IsLeftAvailable==false||(floodfill[currentfloor][ForwardX][ForwardY]<=floodfill[currentfloor][LeftX][LeftY]))){
    Wobble();
  } else if(IsBackwardsAvailable==true && ((IsRightAvailable==false&&IsLeftAvailable==false&&IsForwardAvailable==false)||(floodfill[currentfloor][BackwardsX][BackwardsY]==0))){
    TurnBackwards();
  } else {
    TurnLeft();
  }
}

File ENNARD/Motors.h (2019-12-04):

#include <Servo.h>
#define DeployerPin 46
Servo Deployer;
#define motorUL 5
#define motorULdirA 2
#define motorULdirB 4
#define motorLL 8
#define motorLLdirA 10
#define motorLLdirB 9
#define motorUR 7
#define motorURdirA 6
#define motorURdirB 3
#define motorLR 11
#define motorLRdirA 40
#define motorLRdirB 12
int KitCounter=0;

void MotorsStop(){
  digitalWrite(motorULdirA, HIGH);
  digitalWrite(motorULdirB, HIGH);
  digitalWrite(motorURdirA, HIGH);
  digitalWrite(motorURdirB, HIGH);
  digitalWrite(motorLLdirA, HIGH);
  digitalWrite(motorLLdirB, HIGH);
  digitalWrite(motorLRdirA, HIGH);
  digitalWrite(motorLRdirB, HIGH);
  delay(50);
}

void MotorsInitialize(){
  Deployer.attach(DeployerPin);
  Deployer.write(60);
  pinMode(motorUL, OUTPUT);
  pinMode(motorULdirA, OUTPUT);
  pinMode(motorULdirB, OUTPUT);
  pinMode(motorLL, OUTPUT);
  pinMode(motorLLdirA, OUTPUT);
  pinMode(motorLLdirB, OUTPUT);
  pinMode(motorUR, OUTPUT);
  pinMode(motorURdirA, OUTPUT);
  pinMode(motorURdirB, OUTPUT);
  pinMode(motorLR, OUTPUT);
  pinMode(motorLRdirA, OUTPUT);
  pinMode(motorLRdirB, OUTPUT);
  MotorsStop();
}

void URForward(){
  digitalWrite(motorURdirA, HIGH);
  digitalWrite(motorURdirB, LOW);
}

void URBackwards(){
  digitalWrite(motorURdirA, LOW);
  digitalWrite(motorURdirB, HIGH);
}

void ULForward(){
  digitalWrite(motorULdirA, HIGH);
  digitalWrite(motorULdirB, LOW);
}

void ULBackwards(){
  digitalWrite(motorULdirA, LOW);
  digitalWrite(motorULdirB, HIGH);
}

void LRForward(){
  digitalWrite(motorLRdirA, HIGH);
  digitalWrite(motorLRdirB, LOW);
}

void LRBackwards(){
  digitalWrite(motorLRdirA, LOW);
  digitalWrite(motorLRdirB, HIGH);
}

void LLForward(){
  digitalWrite(motorLLdirA, HIGH);
  digitalWrite(motorLLdirB, LOW);
}

void LLBackwards(){
  digitalWrite(motorLLdirA, LOW);
  digitalWrite(motorLLdirB, HIGH);
}


void MoveForward(int speed){
  ULForward();
  LLForward();
  URForward();
  LRForward();
  analogWrite(motorUL, speed);
  analogWrite(motorLL, speed);
  analogWrite(motorUR, speed);
  analogWrite(motorLR, speed);
}


void MoveForwardPID(int speed){
  ULForward();
  LLForward();
  URForward();
  LRForward();
  CalculatePID();
  analogWrite(motorUL, constrain(speed+PID_value, 130, 255));
  analogWrite(motorLL, constrain(speed+PID_value, 130, 255));
  analogWrite(motorUR, constrain(speed-PID_value, 130, 255));
  analogWrite(motorLR, constrain(speed-PID_value, 130, 255));
}


void MoveBackwards(int speed){
  ULBackwards();
  LLBackwards();
  URBackwards();
  LRBackwards();
  analogWrite(motorUL, speed);
  analogWrite(motorLL, speed);
  analogWrite(motorUR, speed);
  analogWrite(motorLR, speed);
}


void RotateLeft(int speed){
  ULBackwards();
  LLBackwards();
  URForward();
  LRForward();
  analogWrite(motorUL, speed);
  analogWrite(motorLL, speed);
  analogWrite(motorUR, speed);
  analogWrite(motorLR, speed);
}


void RotateRight(int speed){
  ULForward();
  LLForward();
  URBackwards();
  LRBackwards();
  analogWrite(motorUL, speed);
  analogWrite(motorLL, speed);
  analogWrite(motorUR, speed);
  analogWrite(motorLR, speed);
}


void IntroduceRight(int speed){
  ULForward();
  LLForward();
  analogWrite(motorUL, speed);
  analogWrite(motorLL, speed);
  analogWrite(motorUR, 0);
  analogWrite(motorLR, 0);
}


void IntroduceLeft(int speed){
  URForward();
  LRForward();
  analogWrite(motorUL, 0);
  analogWrite(motorLL, 0);
  analogWrite(motorUR, speed);
  analogWrite(motorLR, speed);
}


void DeployKitLeft(){
  Deployer.write(120);
  delay(500);
  Deployer.write(30);
  delay(500);
  Deployer.write(60);
  delay(500);
  KitCounter++;
  delay(100);
}

void DeployKitRight(){
  Deployer.write(0);
  delay(500);
  Deployer.write(90);
  delay(500);
  Deployer.write(60);
  delay(500);
  KitCounter++;
  delay(100);
}

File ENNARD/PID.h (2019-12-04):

#define Kp 100
#define Ki 0
#define Kd 0
float previous_error=0;
float P=0;
float I=0;
float previous_I=0;
float D=0;
float PID_value=0;
float error=0;

void CalculatePID(){
  if(USLeftA<30 && USRightA<30){
  	error=USRightA-USLeftA;
  } else if(USBackA<99 && USBackB<99){
    error = USBackB-USBackA;
  } else if(USFrontA<99 && USFrontB<99 && USFrontCT<99){
    error = USFrontA-USFrontB;
  } else if(USLeftA<99 && USLeftB<99){
    error = USLeftB-USLeftA+(15-USLeftA);
  } else if(USRightA<30 && USRightB<30){
    error = USRightA-USRightB+(USRightA-15);
  } else {
    error = 0;
  }
  if(abs(error)<=0.6){
    error=0;
  }
  P = error;
  I = I + error;
  D = error - previous_error;
  PID_value = round((Kp*P)+(Ki*I)+(Kd*D));
  previous_error=error;
}

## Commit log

2019-12-04 Files used for CAD
    [16x2 Lcd display dsgn arch 2016-edit-00.SLDPRT, 3mm_bolt.SLDPRT, 3x35_screw.SLDPRT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]
2019-12-04 Arduino Testing
